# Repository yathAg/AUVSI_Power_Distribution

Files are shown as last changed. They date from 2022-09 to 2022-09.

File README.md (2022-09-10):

# AUVSI_Power_Distribution

This project includes the PCBS designed for the Seraphim , the Hex-rotor by PROJECT MANAS that participated in AUVSI SUAS 2022

The unavailibility of cheap and reliable power distribution systems called for designing a fully custom solution that powers the following :-
- Six T-Motor P60 170 Kv motors
- PixHawk Cube Orange
- RFD900X Telemetry Radio
- UGV Winch mechanism

The onboard electronic components are powered by
- Two 6S 32000 mAh LiPO Batteries for the Motors
- One 3S 4200 mAh LiPO Battery for control electronics

**The project includes three pcbs:**

## Power distribution pcb

A simple distributor pcb which can have upto 12 motors:
2 Oz thickness for more current
Exposed copper for heat sink
Voltage sense capability using the voltage from balance connector
Mosfets to shut down current flow when required

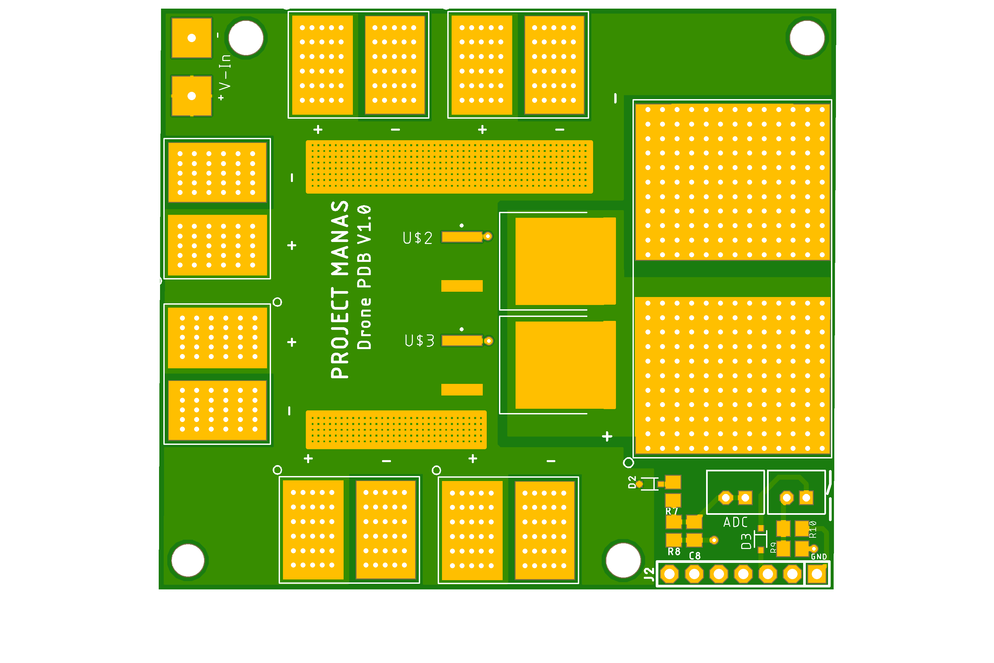
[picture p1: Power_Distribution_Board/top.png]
Power Distribution Board


## Current sensing pcb  
This pcb is based on the allegro asc772 current sensor
The 400 amp variant was avoided due to unavailability
The 200 amp variant was chosen
2 boards will be used in order to measure separate packs in parallel
Output is a analog value of 5v
The board can also measure voltage levels

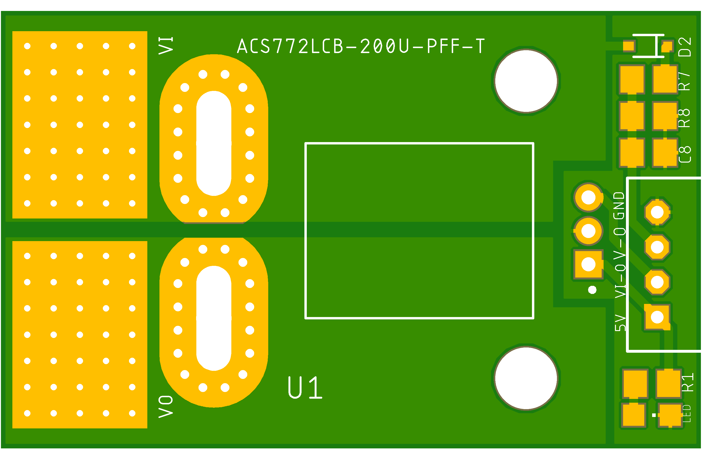
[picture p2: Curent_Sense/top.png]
Curent Sense PCB


## Power HUB

This pcb incorporates the buck and boost modules
1x5v buck ( df13)
2x 5v buck ( ph)
1x 7.4v buck
Current sense mixer

The lmr33640 ic was chosen due to wide input range and 4 amp current output
All bucks were separated
Low space design
Can mix to current sensor values using opamp circuit
Reverse polarity protection

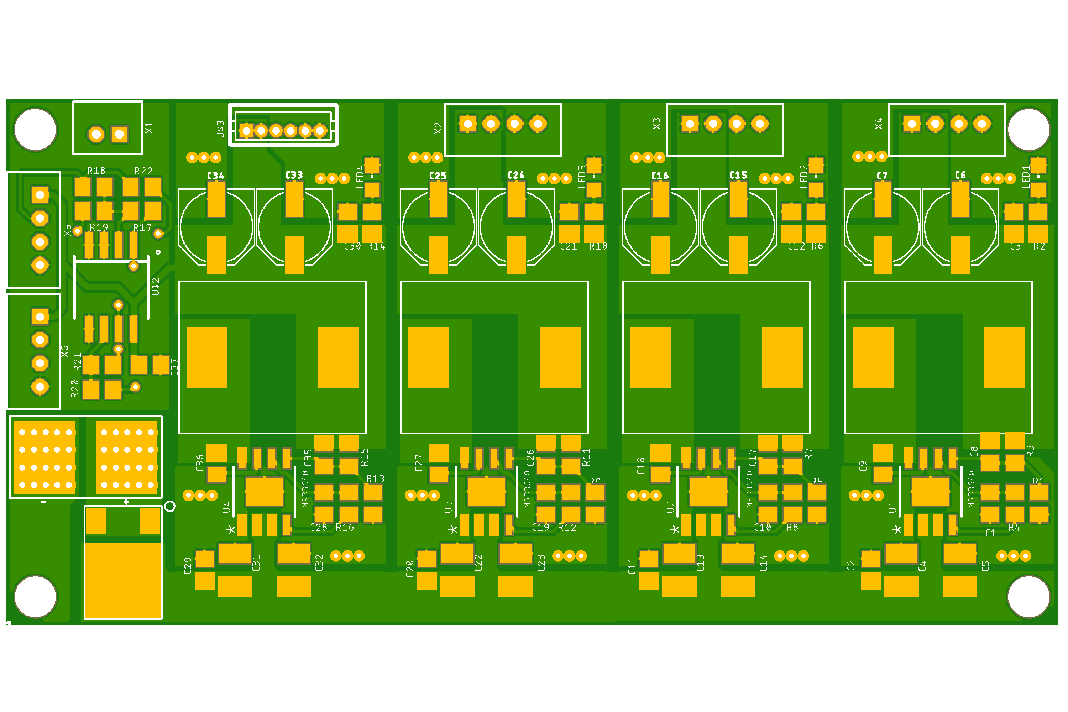
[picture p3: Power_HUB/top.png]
Power HUB


## Pcb design learnings from the project
- No thermals in high current pads
- Avoid choke points ( traces that make current flow path longer)
- Switching loops of power converters have to be as small as possible
- output trace thickness
- Placement of decoupling caps
- Using keepots to avoid traces being to close
- Appropriate pad sizes with vias for current conduction

All schematics , pcb images, and gerber files have been added
The gerbers were formatted for panelization

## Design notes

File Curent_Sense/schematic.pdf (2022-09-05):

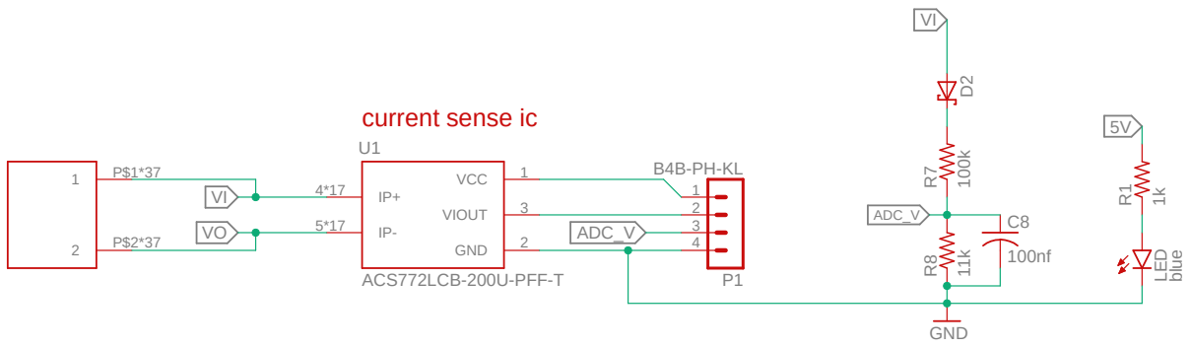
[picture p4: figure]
ACS772LCB-200U-PFF-T; GND; 1k blue; VCC; VIOUT; LED; ADC_V; current sense ic

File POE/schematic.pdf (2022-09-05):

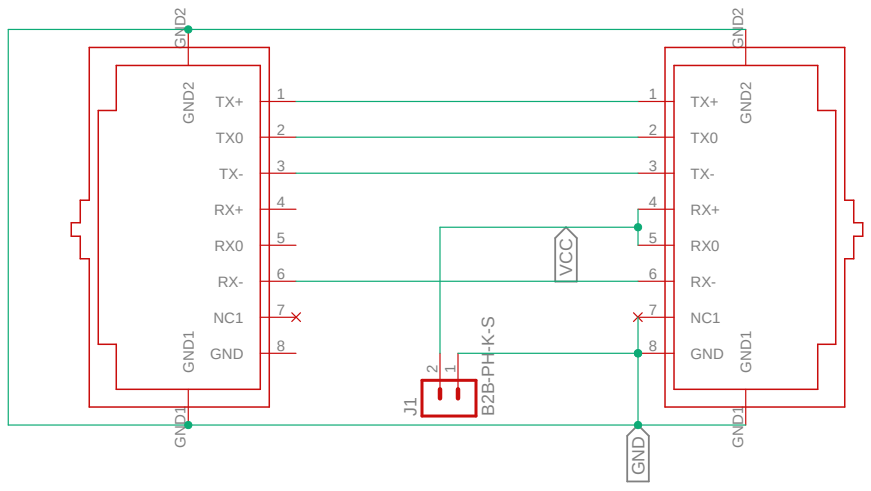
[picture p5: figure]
GND; 8 GND² GND² GND¹ GND¹; GND² GND² GND¹ GND¹ ²¹ J1; GND VCC

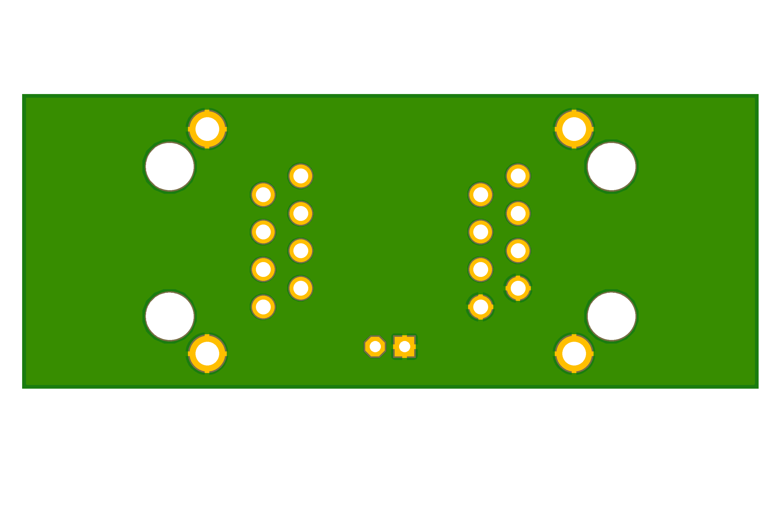
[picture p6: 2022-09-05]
POE/bottom.png

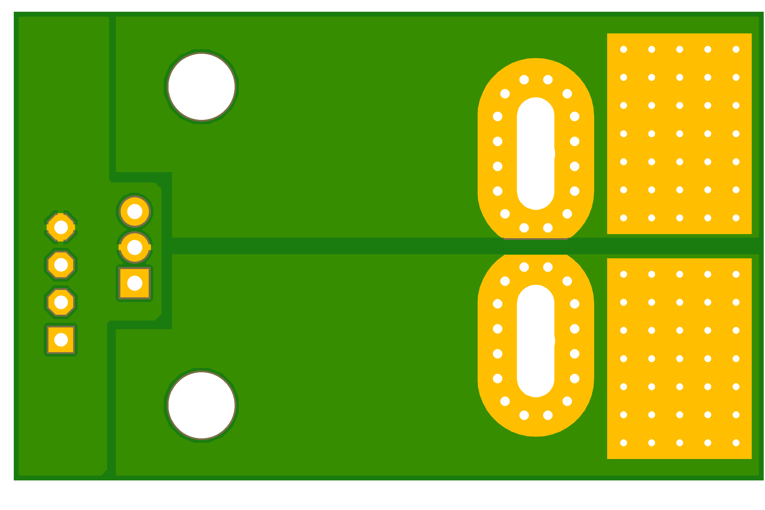
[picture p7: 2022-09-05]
Curent_Sense/bottom.png

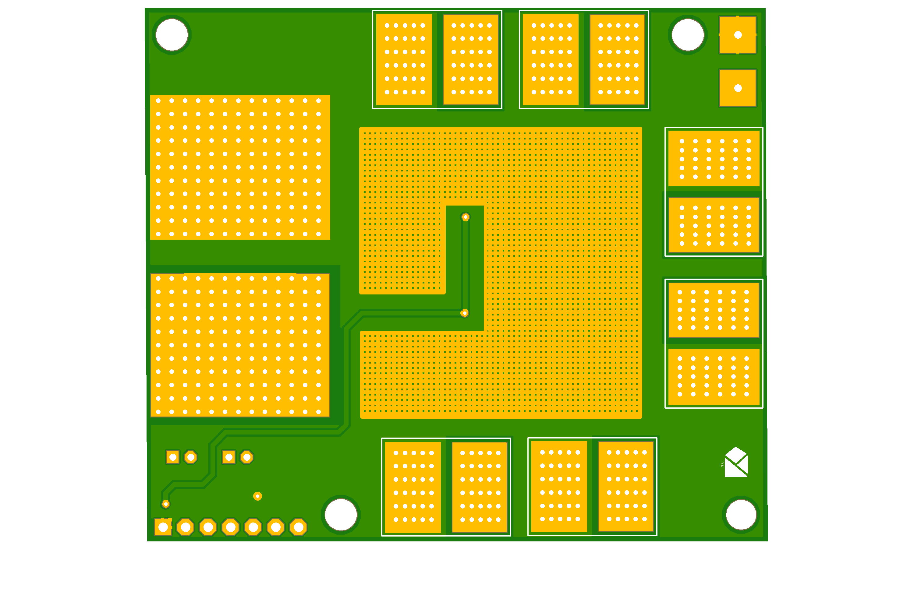
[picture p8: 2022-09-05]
Power_Distribution_Board/bottom.png

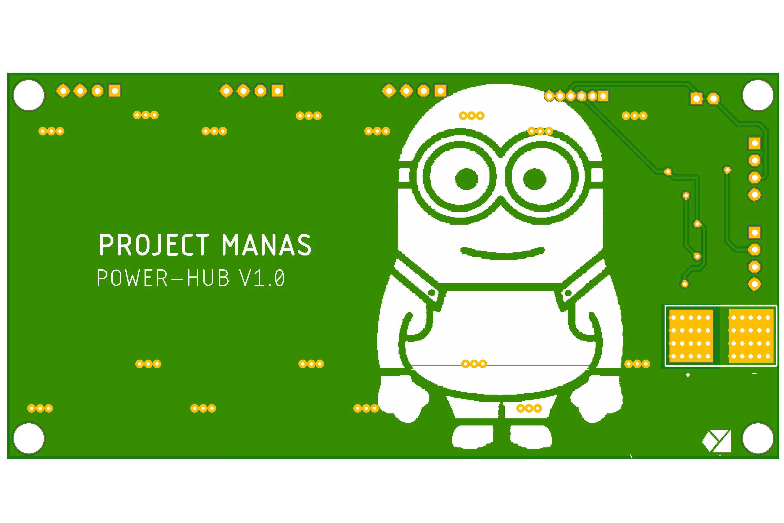
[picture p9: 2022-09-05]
Power_HUB/bottom.png

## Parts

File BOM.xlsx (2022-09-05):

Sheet: pdb
Qty | Value | Device | Package | Parts | Description
1 | 100k | R-US_R0805 | R0805 | R7 | RESISTOR, American symbol
1 | 100nf | C-USC0805 | C0805 | C8 | CAPACITOR, American symbol
1 | 11k | R-US_R0805 | R0805 | R8 | RESISTOR, American symbol
2 | 1PS76SB70,115 | 1PS76SB70,115 | SOD323(F) | D2, D3 | General-purpose Schottky diode General-purpose Schottky diodes in small Surface-Mounted Device (SMD) plastic
2 | 1k | R-US_R0805 | R0805 | R9, R10 | RESISTOR, American symbol
1 | B2B-PH-K-S | B2B-PH-K-S | B2B-PH-K-S | P2 | JST PH series header 2.00mm pitch disconnectable crimp style connectors, vertical (side entry type), 2 pins
1 | B2B-PH-KL | B2B-PH-KL | B2B-PH-K-S | P3 | JST PH series header 2.00mm pitch disconnectable crimp style connectors, vertical (side entry type), 2 pins
1 | F-1X07-SIP-100-40 | F-1X07-SIP-100-40 | SIP-100-07-40 | J2 | FEMALE HEADER
2 | IRFS7730 | IRFS7730 | TO254P1524X457-3N | U$2, U$3

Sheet: current sense
Qty | Value | Device | Package | Parts | Description
1 | 100k | R-US_R0805 | R0805 | R7 | RESISTOR, American symbol
1 | 100nf | C-USC0805 | C0805 | C8 | CAPACITOR, American symbol
1 | 11k | R-US_R0805 | R0805 | R8 | RESISTOR, American symbol
1 | 1PS76SB70,115 | 1PS76SB70,115 | SOD323(F) | D2 | General-purpose Schottky diode General-purpose Schottky diodes in small Surface-Mounted Device (SMD) plastic
1 | 1k | R-US_R0805 | R0805 | R1 | RESISTOR, American symbol
1 | ACS772LCB-200U-PFF-T | ACS772LCB-100U-PFF-T | XDCR_ACS772LCB-100U-PFF-T | U1 | Current Sensor 100A 1 Channel Hall Effect Unidirectional 5-CB Formed Leads, PFF Check prices
1 | B4B-PH-KL | B4B-PH-KL | B4B-PH-K-S | P1 | JST PH series header 2.00mm pitch disconnectable crimp style connectors, vertical (side entry type), 4 pins
1 | blue | LEDCHIPLED_0805 | CHIPLED_0805 | LED | LED

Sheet: poe
Qty | Value | Device | Package | Parts | Description
1 | B2B-PH-K-S | B2B-PH-K-S | B2B-PH-K-S | J1 | JST PH series header 2.00mm pitch disconnectable crimp style connectors, vertical (side entry type), 2 pins
2 | RJ45-TRAFO | RJ45-TRAFO | RJ45-TRAFO | U$1, U$2 | RJ45 socket with integrated magnetics

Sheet: powerhub
Qty | Value | Device | Package | Parts | Description
8 | 100k | R-US_R0805 | R0805 | R3, R4, R7, R8, R11, R12, R15, R16 | RESISTOR, American symbol
9 | 100nf | C-EUC0805 | C0805 | C3, C9, C12, C18, C21, C27, C30, C36, C37 | CAPACITOR, European symbol
8 | 100uF | 100UF-POLAR-25V-20%(ELEC) | PANASONIC_D | C6, C7, C15, C16, C24, C25, C33, C34 | 100µF polarized capacitors
8 | 10uf | C-EUC1210 | C1210 | C4, C5, C13, C14, C22, C23, C31, C32 | CAPACITOR, European symbol
1 | 10uh | INDUCTORINDUCTOR-1265 | INDUCTOR-1265 | I1 | 1260 wurth elektronics
4 | 11k | R-US_R0805 | R0805 | R17, R18, R19, R20 | RESISTOR, American symbol
1 | 15.6k | R-US_R0805 | R0805 | R1 | RESISTOR, American symbol
4 | 1k | R-US_R0805 | R0805 | R2, R6, R10, R14 | RESISTOR, American symbol
4 | 1uf | C-EUC0805 | C0805 | C1, C10, C19, C28 | CAPACITOR, European symbol
4 | 220nf | C-EUC0805 | C0805 | C2, C11, C20, C29 | CAPACITOR, European symbol
1 | 22k | R-US_R0805 | R0805 | R21 | RESISTOR, American symbol
4 | 22pf | C-EUC0805 | C0805 | C8, C17, C26, C35 | CAPACITOR, European symbol
3 | 24.9k | R-US_R0805 | R0805 | R5, R9, R13 | RESISTOR, American symbol
3 | 6.8uh | INDUCTORINDUCTOR-1265 | INDUCTOR-1265 | I2, I3, I4 | 1260 wurth elektronics
1 | B2B-PH-KL | B2B-PH-KL | B2B-PH-K-S | X1 | JST PH series header 2.00mm pitch disconnectable crimp style connectors, vertical (side entry type), 2 pins
5 | B4B-PH-KL | B4B-PH-KL | B4B-PH-K-S | X2, X3, X4, X5, X6 | JST PH series header 2.00mm pitch disconnectable crimp style connectors, vertical (side entry type), 4 pins
1 | LM358 | LM358 | SOP-08 | U$2
4 | LMR33640 | LMR33640 | SO-POWERPAD8_DDA_TEX-M | U1, U2, U3, U4
1 | V40PW22C-M3/I | DIODE-TO252 | TO-252AE | U$1
4 | blue | LEDCHIPLED_0805 | CHIPLED_0805 | LED1, LED2, LED3, LED4 | LED

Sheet: total
Qty for 1 set | Value | Device | Package | Description
10 | 100k | R-US_R0805 | R0805 | RESISTOR, American symbol
11 | 100nf | C-EUC0805 | C0805 | CAPACITOR, European symbol
8 | 100uF | 100UF-POLAR-25V-20%(ELEC) | PANASONIC_D | 100µF polarized capacitors
8 | 10uf | C-EUC1210 | C1210 | CAPACITOR, European symbol
1 | 10uh | INDUCTORINDUCTOR-1265 | INDUCTOR-1265 | 1260 wurth elektronics ( or any similar)
6 | 11k | R-US_R0805 | R0805 | RESISTOR, American symbol
1 | 15.6k | R-US_R0805 | R0805 | RESISTOR, American symbol
7 | 1k | R-US_R0805 | R0805 | RESISTOR, American symbol
4 | 1uf | C-EUC0805 | C0805 | CAPACITOR, European symbol
4 | 220nf | C-EUC0805 | C0805 | CAPACITOR, European symbol
1 | 22k | R-US_R0805 | R0805 | RESISTOR, American symbol
4 | 22pf | C-EUC0805 | C0805 | CAPACITOR, European symbol
3 | 24.9k | R-US_R0805 | R0805 | RESISTOR, American symbol
3 | 6.8uh | INDUCTORINDUCTOR-1265 | INDUCTOR-1265 | 1260 wurth elektronics ( or any similar)
1 | ACS772LCB-200U-PFF-T | ACS772LCB-100U-PFF-T | XDCR_ACS772LCB-100U-PFF-T | Current Sensor 200A 1 Channel Hall Effect Unidirectional 5-CB Formed Leads, PFF ( or any acs current sense 200 amp 712,758
4 | B2B-PH-KL | B2B-PH-KL | B2B-PH-K-S | JST PH series header 2.00mm pitch disconnectable crimp style connectors, vertical , 2 pins
6 | B4B-PH-KL | B4B-PH-KL | B4B-PH-K-S | JST PH series header 2.00mm pitch disconnectable crimp style connectors, vertical (side entry type), 4 pins ( or any similar 2mm pitch connector)
5 | blue | LEDCHIPLED_0805 | CHIPLED_0805 | LED
1 | df13
2 | IRFS7730 | IRFS7730 | TO254P1524X457-3N
1 | LM358 | LM358 | SOP-08
4 | LMR33640 | LMR33640 | SO-POWERPAD8_DDA_TEX-M
2 | RJ45-TRAFO | RJ45-TRAFO | RJ45-TRAFO | RJ45 socket with integrated magnetics
3 | schottkey diode | 1PS76SB70,115 | sod123 | General-purpose Schottky diode General-purpose Schottky diodes in small Surface-Mounted Device (SMD) plastic ( or any similar)
1 | V40PW22C-M3/I | DIODE-TO252 | TO-252AE

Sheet: ic
Value | Device | Package | qty | price
LMR33640 | LMR33640 | SO-POWERPAD8_DDA_TEX-M
IRFS7730 | IRFS7730 | TO254P1524X457-3N | 4
ACS772LCB-200U-PFF-T | ACS772LCB-200U-PFF-T | XDCR_ACS772LCB-200U-PFF-T | 2
V40PW22C-M3/I | DIODE-TO252 | TO-252AE | 4
LM358 | LM358 | SOP-08 | 1

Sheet: connectors
Connector | Quantity
Df13 | 5
XT60-Male
XT60-Female
Rj45 Male
Rj45 Female
Xt150
2pin ph
Wire to board | 15
Connector housing | 15
4pin ph
Wire to board | 20
Connector housing | 50
Crimp contacts | 100

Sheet: final smd
part | package | desc | qty | cost | total
22k | R-US_R0805 | R0805 | 100 | 0.2 | 20
100k | R-US_R0805 | R0805 | 100 | 0.2 | 20
1uf | C-EUC0805 | C0805 | 100 | 1 | 100
220nf | C-EUC0805 | C0805 | 100 | 1 | 100
22pf | C-EUC0805 | C0805 | 100 | 1 | 100
24.9k | R-US_R0805 | R0805 | 100 | 1 | 100
15.6k | R-US_R0805 | R0805 | 100 | 1 | 100
100nf | C-EUC0805 | C0805 | 100 | 1 | 100
1k | R-US_R0805 | R0805 | 100 | 1 | 100
11k | R-US_R0805 | R0805 | 100 | 1 | 100
blue | LEDCHIPLED_0805 | CHIPLED_0805 | 100 | 1 | 100
100uF | 100UF-POLAR-25V-20%(ELEC) | PANASONIC_D | 50 | 3.5 | 175
10uf | C-EUC1210 | C1210 | 50 | 4 | 200
6.8uh | INDUCTORINDUCTOR-1265 | 5a | 10 | 35 | 350
10uh | INDUCTORINDUCTOR-1265 | 5a | 5 | 35 | 175
schottkey diode |  | sod123 | 50 | 3 | 150
 |  |  |  | total | 1990

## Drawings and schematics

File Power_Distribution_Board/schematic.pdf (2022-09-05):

## motor pads

A

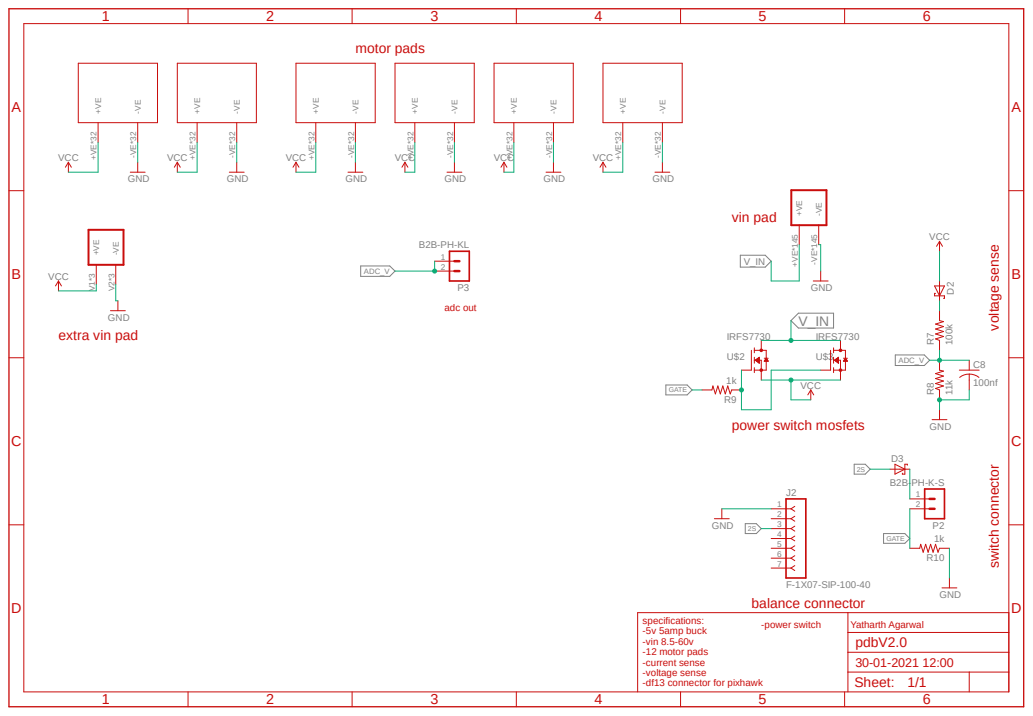
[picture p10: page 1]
VCC; GND; IRFS7730; F-1X07-SIP-100-40; ADC_V; GATE; GATE specifications:; Yatharth Agarwal; vin pad; balance connector; voltage sense; power switch mosfets; switch connector; -power switch; adc out; Sheet:; pdbV2.0

extra vin pad

-5v 5amp buck
-vin 8.5-60v
-12 motor pads
-current sense
-voltage sense
-df13 connector for pixhawk

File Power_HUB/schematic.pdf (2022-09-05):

VIN 2 | EN 3 | PG 4 | VCC 6 | PGND

A

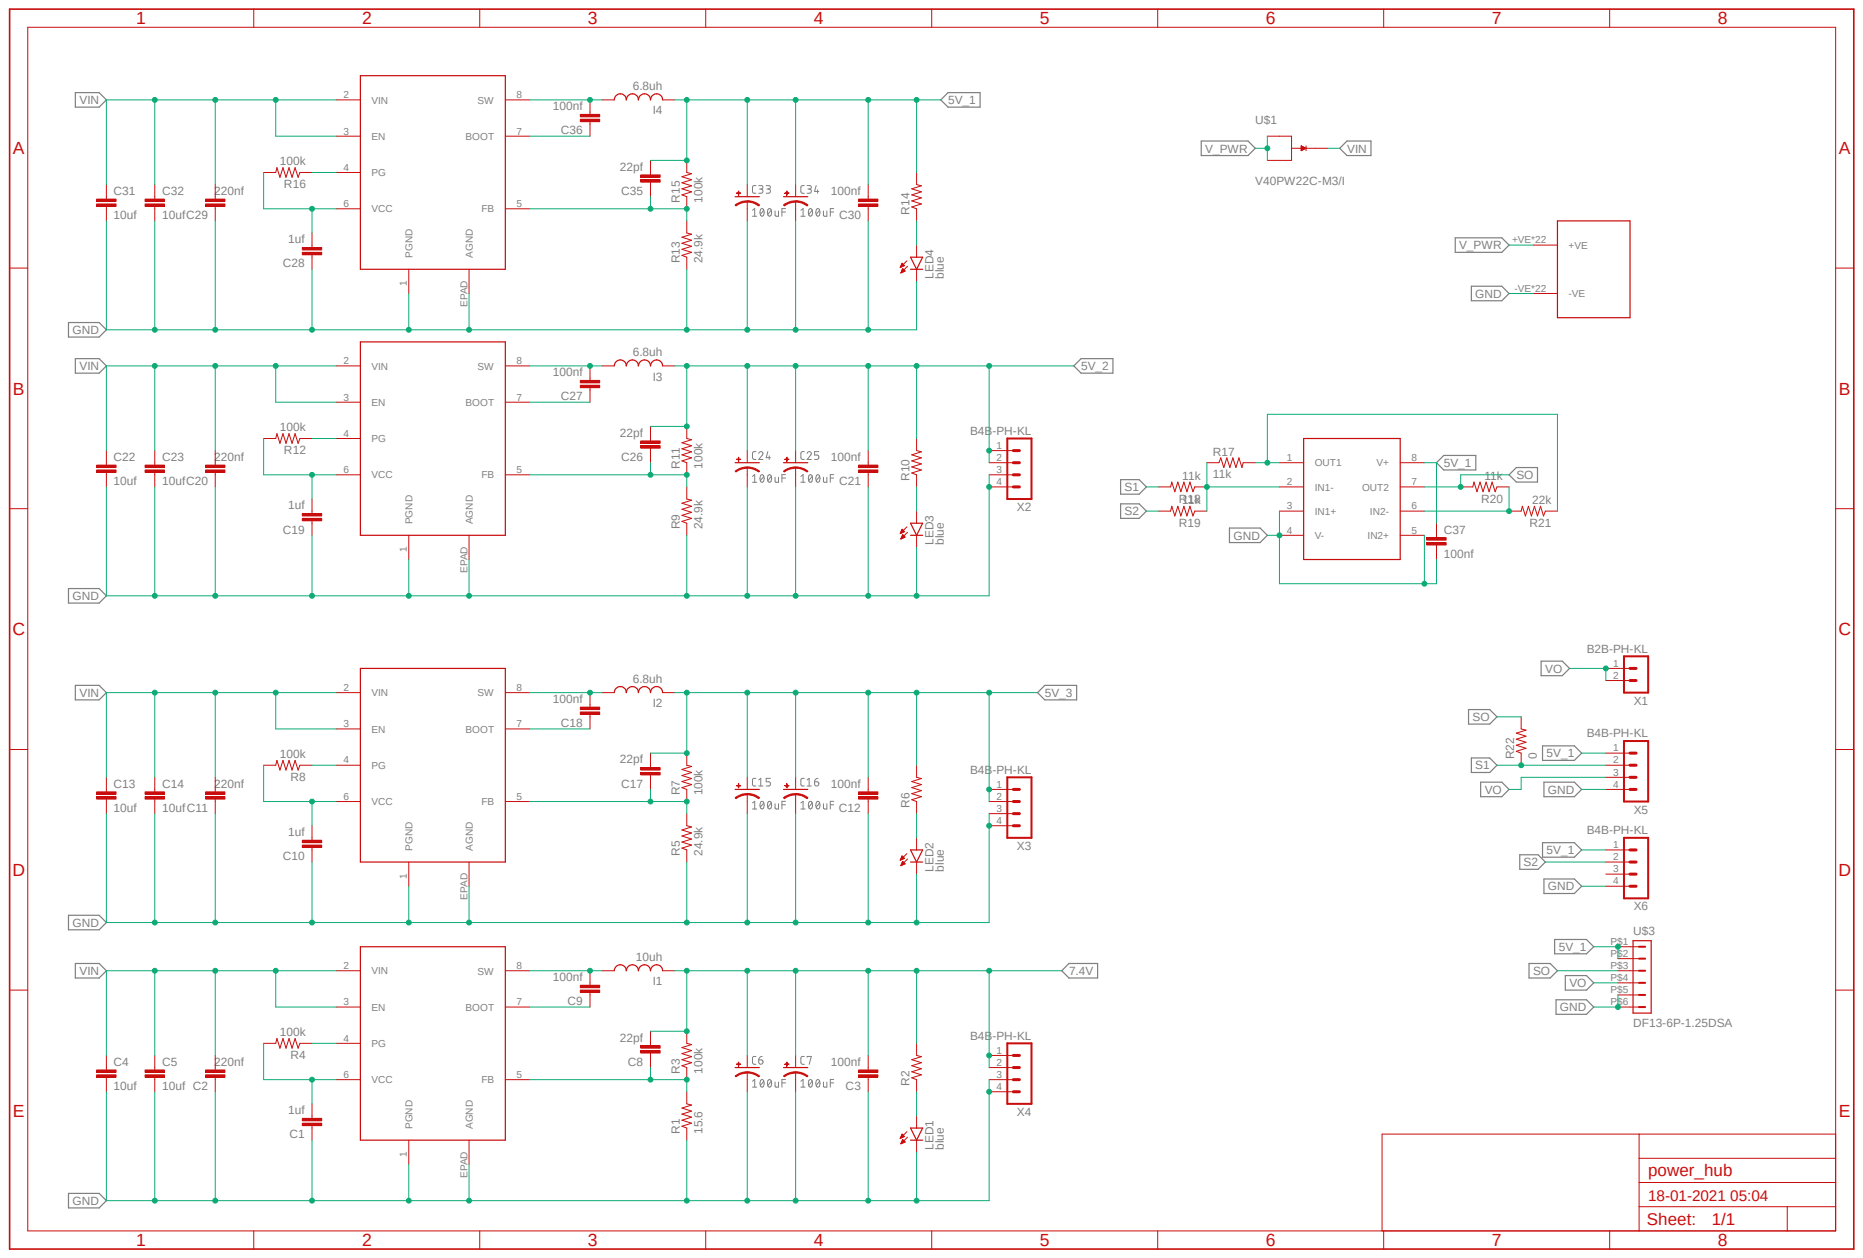
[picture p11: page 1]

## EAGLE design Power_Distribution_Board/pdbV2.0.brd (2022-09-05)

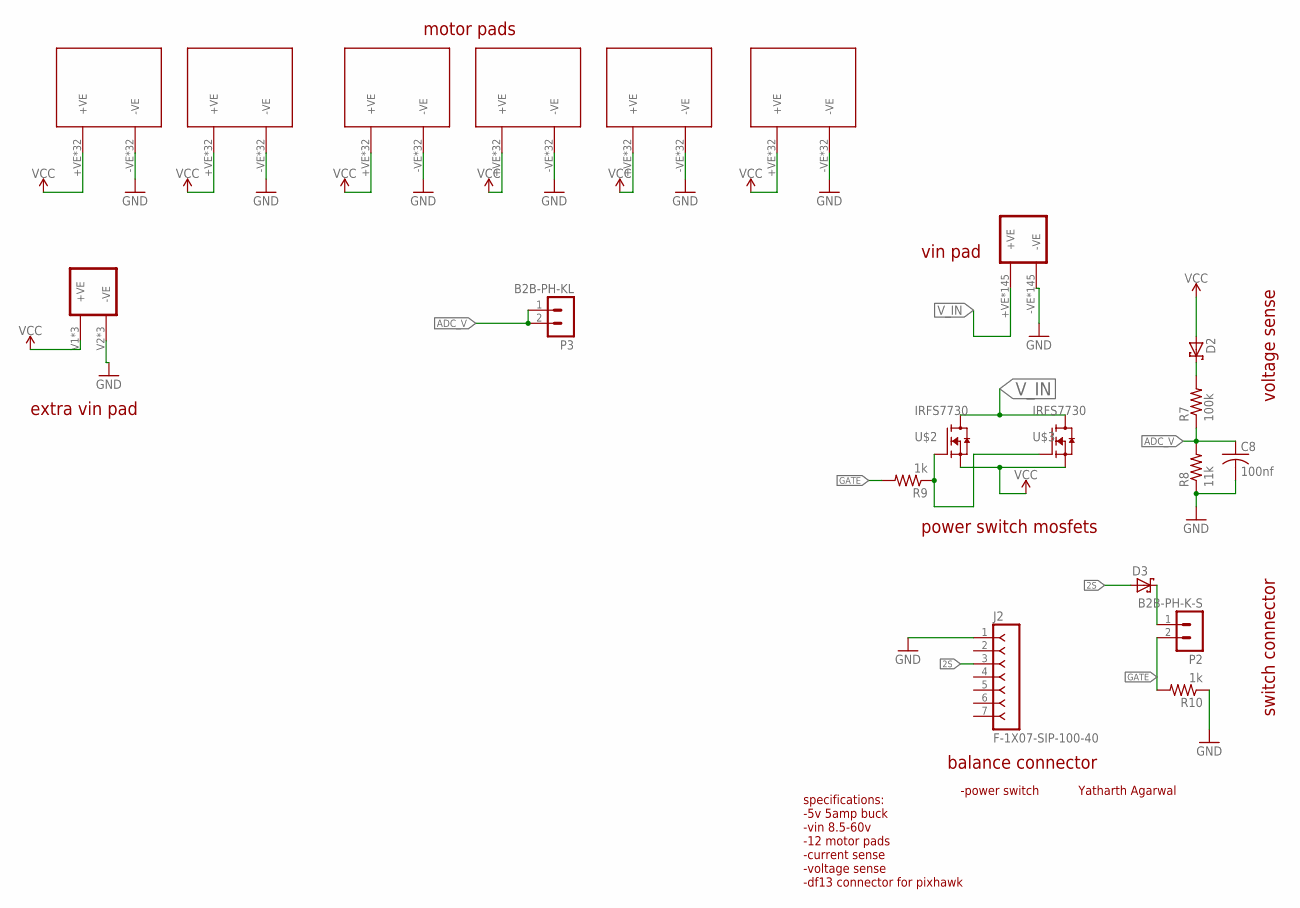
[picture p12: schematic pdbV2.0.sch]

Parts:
C8: 100nf; C0805
D2, D3: 1PS76SB70,115; SOD323(F)
J2: F-1X07-SIP-100-40; SIP-100-07-40
P2: B2B-PH-K-S
P3: B2B-PH-KL; B2B-PH-K-S
R7: 100k; R0805
R8: 11k; R0805
R9, R10: 1k; R0805
T1: BATTERY_PAD
T2, T3, T4, T5, T6, T7: MOTOR_PAD
U$1: CONPAD
U$2, U$3: IRFS7730; TO254P1524X457-3N

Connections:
2S: D3.2 (A), J2.3
ADC_V: C8.1, P3.1, P3.2, R7.1, R8.2
GATE: P2.2, R9.2, R10.2
GND: C8.2, J2.1, R8.1, R10.1, T1.-VE, T1.-VE_1 (-VE), T1.V109 (-VE), T1.V110 (-VE), T1.V111 (-VE), T1.V112 (-VE), T1.V113 (-VE), T1.V114 (-VE), T1.V115 (-VE), T1.V116 (-VE), T1.V117 (-VE), T1.V118 (-VE), T1.V119 (-VE), T1.V121 (-VE), T1.V122 (-VE), T1.V123 (-VE), T1.V124 (-VE), T1.V125 (-VE), T1.V126 (-VE), T1.V127 (-VE), T1.V128 (-VE), T1.V129 (-VE), T1.V130 (-VE), T1.V131 (-VE), T1.V133 (-VE), T1.V134 (-VE), T1.V135 (-VE), T1.V136 (-VE), T1.V137 (-VE), T1.V138 (-VE), T1.V139 (-VE), T1.V140 (-VE), T1.V141 (-VE), T1.V142 (-VE), T1.V143 (-VE), T1.V145 (-VE), T1.V146 (-VE), T1.V147 (-VE), T1.V148 (-VE), T1.V149 (-VE), T1.V150 (-VE), T1.V151 (-VE), T1.V152 (-VE), T1.V153 (-VE), T1.V154 (-VE), T1.V155 (-VE), T1.V157 (-VE), T1.V158 (-VE), T1.V159 (-VE), T1.V160 (-VE), T1.V161 (-VE), T1.V162 (-VE), T1.V163 (-VE), T1.V164 (-VE), T1.V165 (-VE), T1.V166 (-VE), T1.V167 (-VE), T1.V169 (-VE), T1.V170 (-VE), T1.V171 (-VE), T1.V172 (-VE), T1.V173 (-VE), T1.V174 (-VE), T1.V175 (-VE), T1.V176 (-VE), T1.V177 (-VE), T1.V178 (-VE), T1.V179 (-VE), T1.V181 (-VE), T1.V182 (-VE), T1.V183 (-VE), T1.V184 (-VE), T1.V185 (-VE), T1.V186 (-VE), T1.V187 (-VE), T1.V188 (-VE), T1.V189 (-VE), T1.V190 (-VE), T1.V191 (-VE), T1.V193 (-VE), T1.V194 (-VE), T1.V195 (-VE), T1.V196 (-VE), T1.V197 (-VE), T1.V198 (-VE), T1.V199 (-VE), T1.V200 (-VE), T1.V201 (-VE), T1.V202 (-VE), T1.V203 (-VE), T1.V232 (-VE), T1.V233 (-VE), T1.V234 (-VE), T1.V235 (-VE), T1.V236 (-VE), T1.V237 (-VE), T1.V238 (-VE), T1.V239 (-VE), T1.V240 (-VE), T1.V241 (-VE), T1.V242 (-VE), T1.V243 (-VE), T1.V244 (-VE), T1.V245 (-VE), T1.V246 (-VE), T1.V247 (-VE), T1.V248 (-VE), T1.V249 (-VE), T1.V250 (-VE), T1.V251 (-VE), T1.V252 (-VE), T1.V253 (-VE), T1.V254 (-VE), T1.V255 (-VE), T1.V256 (-VE), T1.V257 (-VE), T1.V258 (-VE), T1.V259 (-VE), T1.V260 (-VE), T1.V261 (-VE), T1.V262 (-VE), T1.V263 (-VE), T1.V264 (-VE), T1.V265 (-VE), T1.V266 (-VE), T1.V267 (-VE), T1.V268 (-VE), T1.V269 (-VE), T1.V270 (-VE), T1.V271 (-VE), T1.V272 (-VE), T1.V273 (-VE), T1.V274 (-VE), T1.V275 (-VE), T1.V276 (-VE), T1.V277 (-VE), T1.V278 (-VE), T1.V279 (-VE), T1.V280 (-VE), T1.V281 (-VE), T1.V282 (-VE), T1.V283 (-VE), T1.V284 (-VE), T1.V285 (-VE), T1.V286 (-VE), T2.-VE, T2.-VE_1 (-VE), T2.V32 (-VE), T2.V33 (-VE), T2.V34 (-VE), T2.V35 (-VE), T2.V36 (-VE), T2.V37 (-VE), T2.V38 (-VE), T2.V39 (-VE), T2.V40 (-VE), T2.V41 (-VE), T2.V42 (-VE), T2.V43 (-VE), T2.V44 (-VE), T2.V45 (-VE), T2.V46 (-VE), T2.V47 (-VE), T2.V48 (-VE), T2.V49 (-VE), T2.V50 (-VE), T2.V51 (-VE), T2.V52 (-VE), T2.V53 (-VE), T2.V54 (-VE), T2.V55 (-VE), T2.V56 (-VE), T2.V57 (-VE), T2.V58 (-VE), T2.V59 (-VE), T2.V60 (-VE), T2.V61 (-VE), T3.-VE, T3.-VE_1 (-VE), T3.V32 (-VE), T3.V33 (-VE), T3.V34 (-VE), T3.V35 (-VE), T3.V36 (-VE), T3.V37 (-VE), T3.V38 (-VE), T3.V39 (-VE), T3.V40 (-VE), T3.V41 (-VE), T3.V42 (-VE), T3.V43 (-VE), T3.V44 (-VE), T3.V45 (-VE), T3.V46 (-VE), T3.V47 (-VE), T3.V48 (-VE), T3.V49 (-VE), T3.V50 (-VE), T3.V51 (-VE), T3.V52 (-VE), T3.V53 (-VE), T3.V54 (-VE), T3.V55 (-VE), T3.V56 (-VE), T3.V57 (-VE), T3.V58 (-VE), T3.V59 (-VE), T3.V60 (-VE), T3.V61 (-VE), T4.-VE, T4.-VE_1 (-VE), T4.V32 (-VE), T4.V33 (-VE), T4.V34 (-VE), T4.V35 (-VE), T4.V36 (-VE), T4.V37 (-VE), T4.V38 (-VE), T4.V39 (-VE), T4.V40 (-VE), T4.V41 (-VE), T4.V42 (-VE), T4.V43 (-VE), T4.V44 (-VE), T4.V45 (-VE), T4.V46 (-VE), T4.V47 (-VE), T4.V48 (-VE), T4.V49 (-VE), T4.V50 (-VE), T4.V51 (-VE), T4.V52 (-VE), T4.V53 (-VE), T4.V54 (-VE), T4.V55 (-VE), T4.V56 (-VE), T4.V57 (-VE), T4.V58 (-VE), T4.V59 (-VE), T4.V60 (-VE), T4.V61 (-VE), T5.-VE, T5.-VE_1 (-VE), T5.V32 (-VE), T5.V33 (-VE), T5.V34 (-VE), T5.V35 (-VE), T5.V36 (-VE), T5.V37 (-VE), T5.V38 (-VE), T5.V39 (-VE), T5.V40 (-VE), T5.V41 (-VE), T5.V42 (-VE), T5.V43 (-VE), T5.V44 (-VE), T5.V45 (-VE), T5.V46 (-VE), T5.V47 (-VE), T5.V48 (-VE), T5.V49 (-VE), T5.V50 (-VE), T5.V51 (-VE), T5.V52 (-VE), T5.V53 (-VE), T5.V54 (-VE), T5.V55 (-VE), T5.V56 (-VE), T5.V57 (-VE), T5.V58 (-VE), T5.V59 (-VE), T5.V60 (-VE), T5.V61 (-VE), T6.-VE, T6.-VE_1 (-VE), T6.V32 (-VE), T6.V33 (-VE), T6.V34 (-VE), T6.V35 (-VE), T6.V36 (-VE), T6.V37 (-VE), T6.V38 (-VE), T6.V39 (-VE), T6.V40 (-VE), T6.V41 (-VE), T6.V42 (-VE), T6.V43 (-VE), T6.V44 (-VE), T6.V45 (-VE), T6.V46 (-VE), T6.V47 (-VE), T6.V48 (-VE), T6.V49 (-VE), T6.V50 (-VE), T6.V51 (-VE), T6.V52 (-VE), T6.V53 (-VE), T6.V54 (-VE), T6.V55 (-VE), T6.V56 (-VE), T6.V57 (-VE), T6.V58 (-VE), T6.V59 (-VE), T6.V60 (-VE), T6.V61 (-VE), T7.-VE, T7.-VE_1 (-VE), T7.V32 (-VE), T7.V33 (-VE), T7.V34 (-VE), T7.V35 (-VE), T7.V36 (-VE), T7.V37 (-VE), T7.V38 (-VE), T7.V39 (-VE), T7.V40 (-VE), T7.V41 (-VE), T7.V42 (-VE), T7.V43 (-VE), T7.V44 (-VE), T7.V45 (-VE), T7.V46 (-VE), T7.V47 (-VE), T7.V48 (-VE), T7.V49 (-VE), T7.V50 (-VE), T7.V51 (-VE), T7.V52 (-VE), T7.V53 (-VE), T7.V54 (-VE), T7.V55 (-VE), T7.V56 (-VE), T7.V57 (-VE), T7.V58 (-VE), T7.V59 (-VE), T7.V60 (-VE), T7.V61 (-VE), U$1.V2 (-VE), U$1.V4 (-VE), U$1.V6 (-VE)
unnamed: D3.1 (K), P2.1
unnamed: D2.1 (K), R7.2
unnamed: R9.1, U$2.1 (G), U$3.1 (G)
VCC: D2.2 (A), T2.+VE, T2.+VE_1 (+VE), T2.V1 (+VE), T2.V3 (+VE), T2.V4 (+VE), T2.V5 (+VE), T2.V6 (+VE), T2.V7 (+VE), T2.V8 (+VE), T2.V9 (+VE), T2.V10 (+VE), T2.V11 (+VE), T2.V12 (+VE), T2.V13 (+VE), T2.V14 (+VE), T2.V15 (+VE), T2.V16 (+VE), T2.V17 (+VE), T2.V18 (+VE), T2.V19 (+VE), T2.V20 (+VE), T2.V21 (+VE), T2.V22 (+VE), T2.V23 (+VE), T2.V24 (+VE), T2.V25 (+VE), T2.V26 (+VE), T2.V27 (+VE), T2.V28 (+VE), T2.V29 (+VE), T2.V30 (+VE), T2.V31 (+VE), T3.+VE, T3.+VE_1 (+VE), T3.V1 (+VE), T3.V3 (+VE), T3.V4 (+VE), T3.V5 (+VE), T3.V6 (+VE), T3.V7 (+VE), T3.V8 (+VE), T3.V9 (+VE), T3.V10 (+VE), T3.V11 (+VE), T3.V12 (+VE), T3.V13 (+VE), T3.V14 (+VE), T3.V15 (+VE), T3.V16 (+VE), T3.V17 (+VE), T3.V18 (+VE), T3.V19 (+VE), T3.V20 (+VE), T3.V21 (+VE), T3.V22 (+VE), T3.V23 (+VE), T3.V24 (+VE), T3.V25 (+VE), T3.V26 (+VE), T3.V27 (+VE), T3.V28 (+VE), T3.V29 (+VE), T3.V30 (+VE), T3.V31 (+VE), T4.+VE, T4.+VE_1 (+VE), T4.V1 (+VE), T4.V3 (+VE), T4.V4 (+VE), T4.V5 (+VE), T4.V6 (+VE), T4.V7 (+VE), T4.V8 (+VE), T4.V9 (+VE), T4.V10 (+VE), T4.V11 (+VE), T4.V12 (+VE), T4.V13 (+VE), T4.V14 (+VE), T4.V15 (+VE), T4.V16 (+VE), T4.V17 (+VE), T4.V18 (+VE), T4.V19 (+VE), T4.V20 (+VE), T4.V21 (+VE), T4.V22 (+VE), T4.V23 (+VE), T4.V24 (+VE), T4.V25 (+VE), T4.V26 (+VE), T4.V27 (+VE), T4.V28 (+VE), T4.V29 (+VE), T4.V30 (+VE), T4.V31 (+VE), T5.+VE, T5.+VE_1 (+VE), T5.V1 (+VE), T5.V3 (+VE), T5.V4 (+VE), T5.V5 (+VE), T5.V6 (+VE), T5.V7 (+VE), T5.V8 (+VE), T5.V9 (+VE), T5.V10 (+VE), T5.V11 (+VE), T5.V12 (+VE), T5.V13 (+VE), T5.V14 (+VE), T5.V15 (+VE), T5.V16 (+VE), T5.V17 (+VE), T5.V18 (+VE), T5.V19 (+VE), T5.V20 (+VE), T5.V21 (+VE), T5.V22 (+VE), T5.V23 (+VE), T5.V24 (+VE), T5.V25 (+VE), T5.V26 (+VE), T5.V27 (+VE), T5.V28 (+VE), T5.V29 (+VE), T5.V30 (+VE), T5.V31 (+VE), T6.+VE, T6.+VE_1 (+VE), T6.V1 (+VE), T6.V3 (+VE), T6.V4 (+VE), T6.V5 (+VE), T6.V6 (+VE), T6.V7 (+VE), T6.V8 (+VE), T6.V9 (+VE), T6.V10 (+VE), T6.V11 (+VE), T6.V12 (+VE), T6.V13 (+VE), T6.V14 (+VE), T6.V15 (+VE), T6.V16 (+VE), T6.V17 (+VE), T6.V18 (+VE), T6.V19 (+VE), T6.V20 (+VE), T6.V21 (+VE), T6.V22 (+VE), T6.V23 (+VE), T6.V24 (+VE), T6.V25 (+VE), T6.V26 (+VE), T6.V27 (+VE), T6.V28 (+VE), T6.V29 (+VE), T6.V30 (+VE), T6.V31 (+VE), T7.+VE, T7.+VE_1 (+VE), T7.V1 (+VE), T7.V3 (+VE), T7.V4 (+VE), T7.V5 (+VE), T7.V6 (+VE), T7.V7 (+VE), T7.V8 (+VE), T7.V9 (+VE), T7.V10 (+VE), T7.V11 (+VE), T7.V12 (+VE), T7.V13 (+VE), T7.V14 (+VE), T7.V15 (+VE), T7.V16 (+VE), T7.V17 (+VE), T7.V18 (+VE), T7.V19 (+VE), T7.V20 (+VE), T7.V21 (+VE), T7.V22 (+VE), T7.V23 (+VE), T7.V24 (+VE), T7.V25 (+VE), T7.V26 (+VE), T7.V27 (+VE), T7.V28 (+VE), T7.V29 (+VE), T7.V30 (+VE), T7.V31 (+VE), U$1.V1 (+VE), U$1.V3 (+VE), U$1.V5 (+VE), U$2.3 (S), U$3.3 (S)
V_IN: T1.+VE, T1.+VE_1 (+VE), T1.V1 (+VE), T1.V2 (+VE), T1.V3 (+VE), T1.V4 (+VE), T1.V5 (+VE), T1.V6 (+VE), T1.V7 (+VE), T1.V8 (+VE), T1.V9 (+VE), T1.V10 (+VE), T1.V11 (+VE), T1.V12 (+VE), T1.V13 (+VE), T1.V14 (+VE), T1.V15 (+VE), T1.V16 (+VE), T1.V17 (+VE), T1.V18 (+VE), T1.V19 (+VE), T1.V20 (+VE), T1.V21 (+VE), T1.V22 (+VE), T1.V23 (+VE), T1.V24 (+VE), T1.V25 (+VE), T1.V26 (+VE), T1.V27 (+VE), T1.V28 (+VE), T1.V29 (+VE), T1.V30 (+VE), T1.V31 (+VE), T1.V32 (+VE), T1.V33 (+VE), T1.V34 (+VE), T1.V35 (+VE), T1.V36 (+VE), T1.V37 (+VE), T1.V38 (+VE), T1.V39 (+VE), T1.V40 (+VE), T1.V41 (+VE), T1.V42 (+VE), T1.V43 (+VE), T1.V44 (+VE), T1.V45 (+VE), T1.V46 (+VE), T1.V47 (+VE), T1.V48 (+VE), T1.V49 (+VE), T1.V50 (+VE), T1.V51 (+VE), T1.V52 (+VE), T1.V53 (+VE), T1.V54 (+VE), T1.V55 (+VE), T1.V56 (+VE), T1.V57 (+VE), T1.V58 (+VE), T1.V59 (+VE), T1.V60 (+VE), T1.V61 (+VE), T1.V62 (+VE), T1.V63 (+VE), T1.V64 (+VE), T1.V65 (+VE), T1.V66 (+VE), T1.V67 (+VE), T1.V68 (+VE), T1.V69 (+VE), T1.V70 (+VE), T1.V71 (+VE), T1.V72 (+VE), T1.V73 (+VE), T1.V74 (+VE), T1.V75 (+VE), T1.V76 (+VE), T1.V77 (+VE), T1.V78 (+VE), T1.V79 (+VE), T1.V80 (+VE), T1.V81 (+VE), T1.V82 (+VE), T1.V83 (+VE), T1.V84 (+VE), T1.V85 (+VE), T1.V86 (+VE), T1.V87 (+VE), T1.V88 (+VE), T1.V89 (+VE), T1.V90 (+VE), T1.V91 (+VE), T1.V92 (+VE), T1.V93 (+VE), T1.V94 (+VE), T1.V95 (+VE), T1.V96 (+VE), T1.V97 (+VE), T1.V98 (+VE), T1.V99 (+VE), T1.V100 (+VE), T1.V101 (+VE), T1.V102 (+VE), T1.V103 (+VE), T1.V104 (+VE), T1.V105 (+VE), T1.V106 (+VE), T1.V107 (+VE), T1.V108 (+VE), T1.V120 (+VE), T1.V132 (+VE), T1.V144 (+VE), T1.V156 (+VE), T1.V168 (+VE), T1.V180 (+VE), T1.V192 (+VE), T1.V204 (+VE), T1.V205 (+VE), T1.V206 (+VE), T1.V207 (+VE), T1.V208 (+VE), T1.V209 (+VE), T1.V210 (+VE), T1.V211 (+VE), T1.V212 (+VE), T1.V213 (+VE), T1.V214 (+VE), T1.V215 (+VE), T1.V216 (+VE), T1.V217 (+VE), T1.V218 (+VE), T1.V219 (+VE), T1.V220 (+VE), T1.V221 (+VE), T1.V222 (+VE), T1.V223 (+VE), T1.V224 (+VE), T1.V225 (+VE), T1.V226 (+VE), T1.V227 (+VE), T1.V228 (+VE), T1.V229 (+VE), T1.V230 (+VE), T1.V231 (+VE), U$2.2 (D), U$3.2 (D)

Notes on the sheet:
specifications: -5v 5amp buck -vin 8.5-60v -12 motor pads -current sense -voltage sense -df13 connector for pixhawk
Yatharth Agarwal
motor pads
extra vin pad
vin pad
balance connector
voltage sense
power switch mosfets
switch connector
-power switch

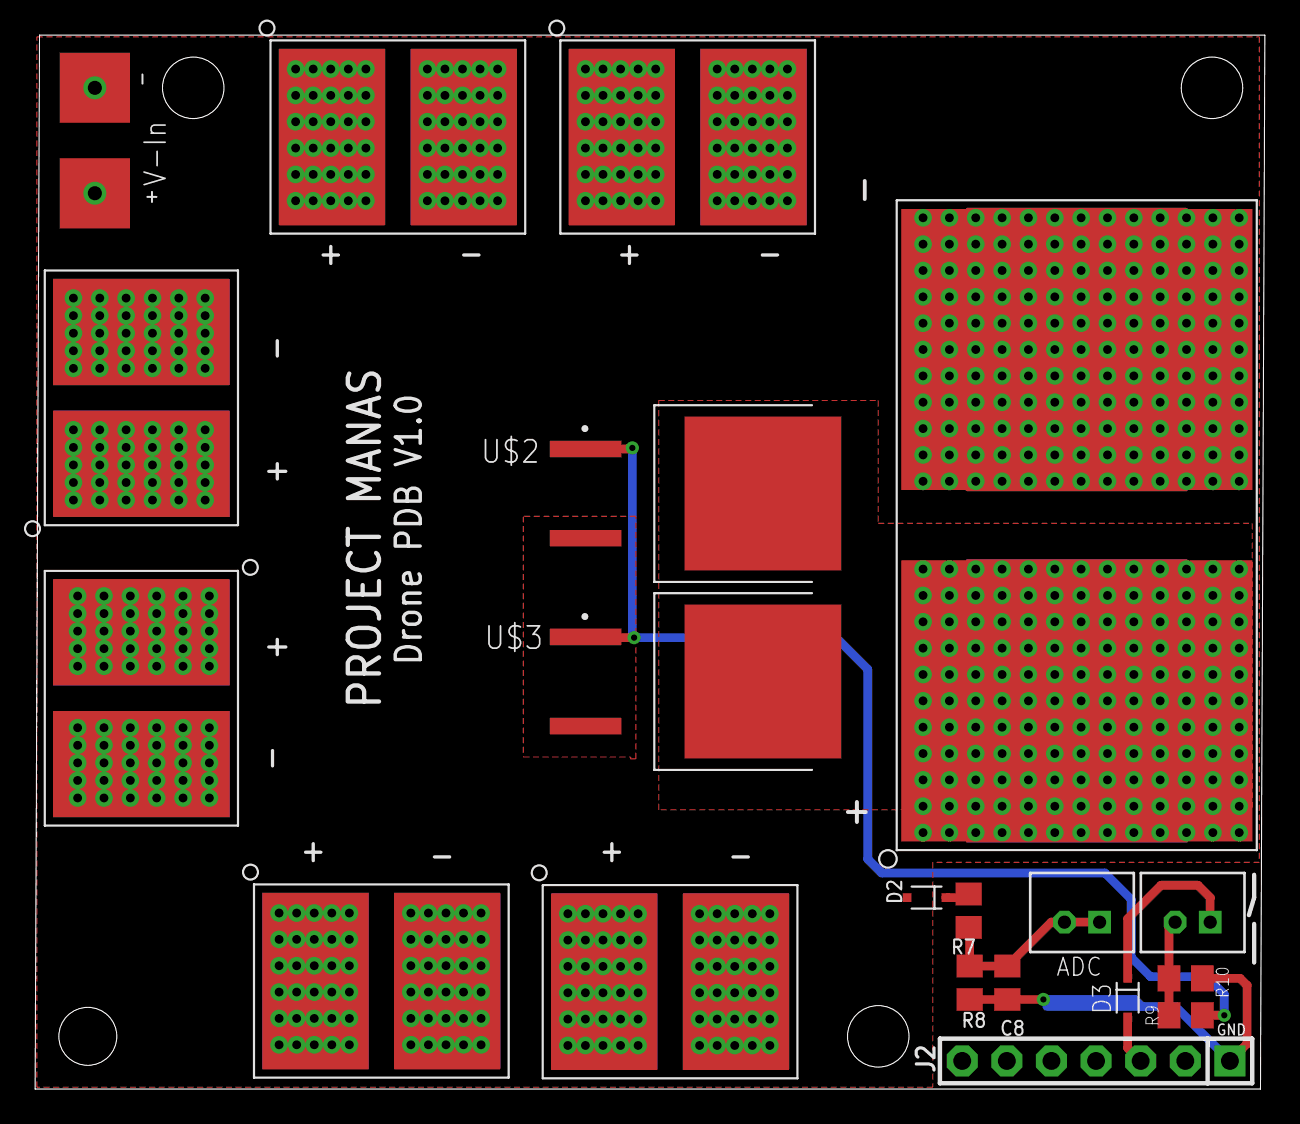
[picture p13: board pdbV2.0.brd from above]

Board: 2 copper layers, 70.0 x 60.0 mm, 20 parts (0 on the bottom side), 9 nets.

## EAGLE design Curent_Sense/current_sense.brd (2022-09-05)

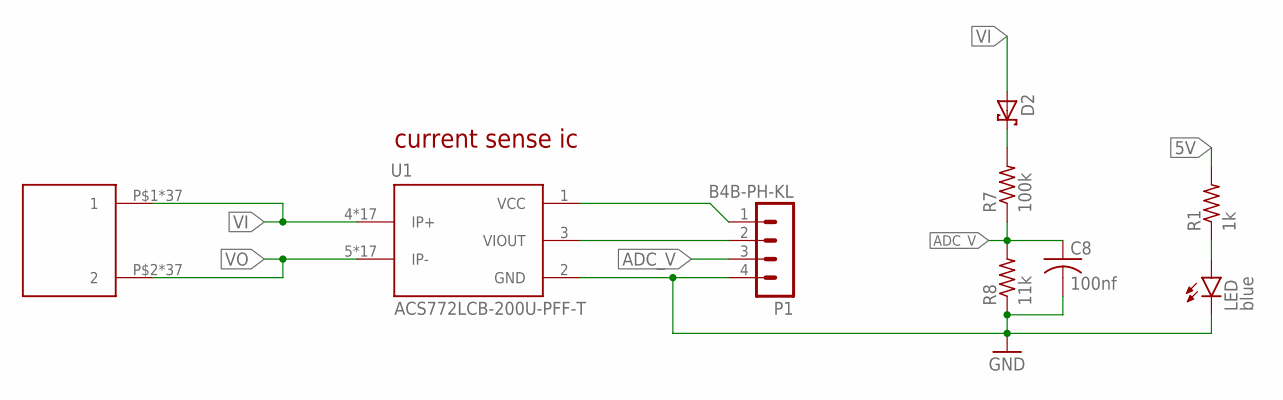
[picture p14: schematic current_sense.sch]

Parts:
C8: 100nf; C0805
D2: 1PS76SB70,115; SOD323(F)
LED: blue; CHIPLED_0805
P1: B4B-PH-KL; B4B-PH-K-S
R1: 1k; R0805
R7: 100k; R0805
R8: 11k; R0805
U1: ACS772LCB-200U-PFF-T; XDCR_ACS772LCB-100U-PFF-T
U$1: CON_PAD

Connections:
5V: P1.1, R1.2, U1.1 (VCC)
ADC_V: C8.1, P1.3, R7.1, R8.2
GND: C8.2, LED.C, P1.4, R8.1, U1.2 (GND)
unnamed: P1.2, U1.3 (VIOUT)
unnamed: LED.A, R1.1
unnamed: D2.1 (K), R7.2
VI: D2.2 (A), U1.4 (IP+), U1.4_1 (IP+), U1.4_2 (IP+), U1.4_3 (IP+), U1.4_4 (IP+), U1.4_5 (IP+), U1.4_6 (IP+), U1.4_7 (IP+), U1.4_8 (IP+), U1.4_9 (IP+), U1.4_10 (IP+), U1.4_11 (IP+), U1.4_12 (IP+), U1.4_13 (IP+), U1.4_14 (IP+), U1.4_15 (IP+), U1.4_16 (IP+), U$1.P$1 (1), U$1.P$3 (1), U$1.P$5 (1), U$1.P$6 (1), U$1.P$7 (1), U$1.P$8 (1), U$1.P$9 (1), U$1.P$10 (1), U$1.P$11 (1), U$1.P$12 (1), U$1.P$13 (1), U$1.P$14 (1), U$1.P$15 (1), U$1.P$16 (1), U$1.P$17 (1), U$1.P$18 (1), U$1.P$19 (1), U$1.P$20 (1), U$1.P$21 (1), U$1.P$22 (1), U$1.P$23 (1), U$1.P$24 (1), U$1.P$25 (1), U$1.P$26 (1), U$1.P$27 (1), U$1.P$28 (1), U$1.P$29 (1), U$1.P$30 (1), U$1.P$31 (1), U$1.P$32 (1), U$1.P$33 (1), U$1.P$34 (1), U$1.P$35 (1), U$1.P$36 (1), U$1.P$37 (1), U$1.P$38 (1), U$1.P$39 (1)
VO: U1.5 (IP-), U1.5_1 (IP-), U1.5_2 (IP-), U1.5_3 (IP-), U1.5_4 (IP-), U1.5_5 (IP-), U1.5_6 (IP-), U1.5_7 (IP-), U1.5_8 (IP-), U1.5_9 (IP-), U1.5_10 (IP-), U1.5_11 (IP-), U1.5_12 (IP-), U1.5_13 (IP-), U1.5_14 (IP-), U1.5_15 (IP-), U1.5_16 (IP-), U$1.P$2 (2), U$1.P$4 (2), U$1.P$40 (2), U$1.P$41 (2), U$1.P$42 (2), U$1.P$43 (2), U$1.P$44 (2), U$1.P$45 (2), U$1.P$46 (2), U$1.P$47 (2), U$1.P$48 (2), U$1.P$49 (2), U$1.P$50 (2), U$1.P$51 (2), U$1.P$52 (2), U$1.P$53 (2), U$1.P$54 (2), U$1.P$55 (2), U$1.P$56 (2), U$1.P$57 (2), U$1.P$58 (2), U$1.P$59 (2), U$1.P$60 (2), U$1.P$61 (2), U$1.P$62 (2), U$1.P$63 (2), U$1.P$64 (2), U$1.P$65 (2), U$1.P$66 (2), U$1.P$67 (2), U$1.P$68 (2), U$1.P$69 (2), U$1.P$70 (2), U$1.P$71 (2), U$1.P$72 (2), U$1.P$73 (2), U$1.P$74 (2)

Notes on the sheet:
current sense ic

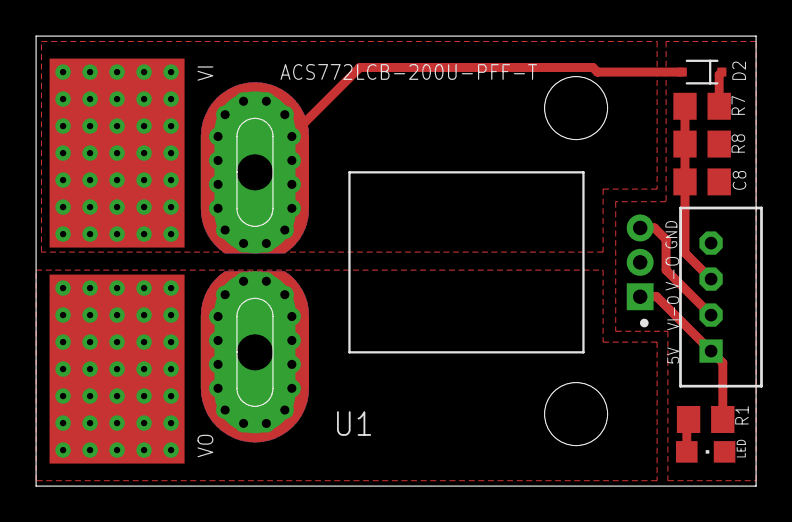
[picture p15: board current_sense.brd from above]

Board: 2 copper layers, 40.0 x 25.0 mm, 9 parts (0 on the bottom side), 8 nets.

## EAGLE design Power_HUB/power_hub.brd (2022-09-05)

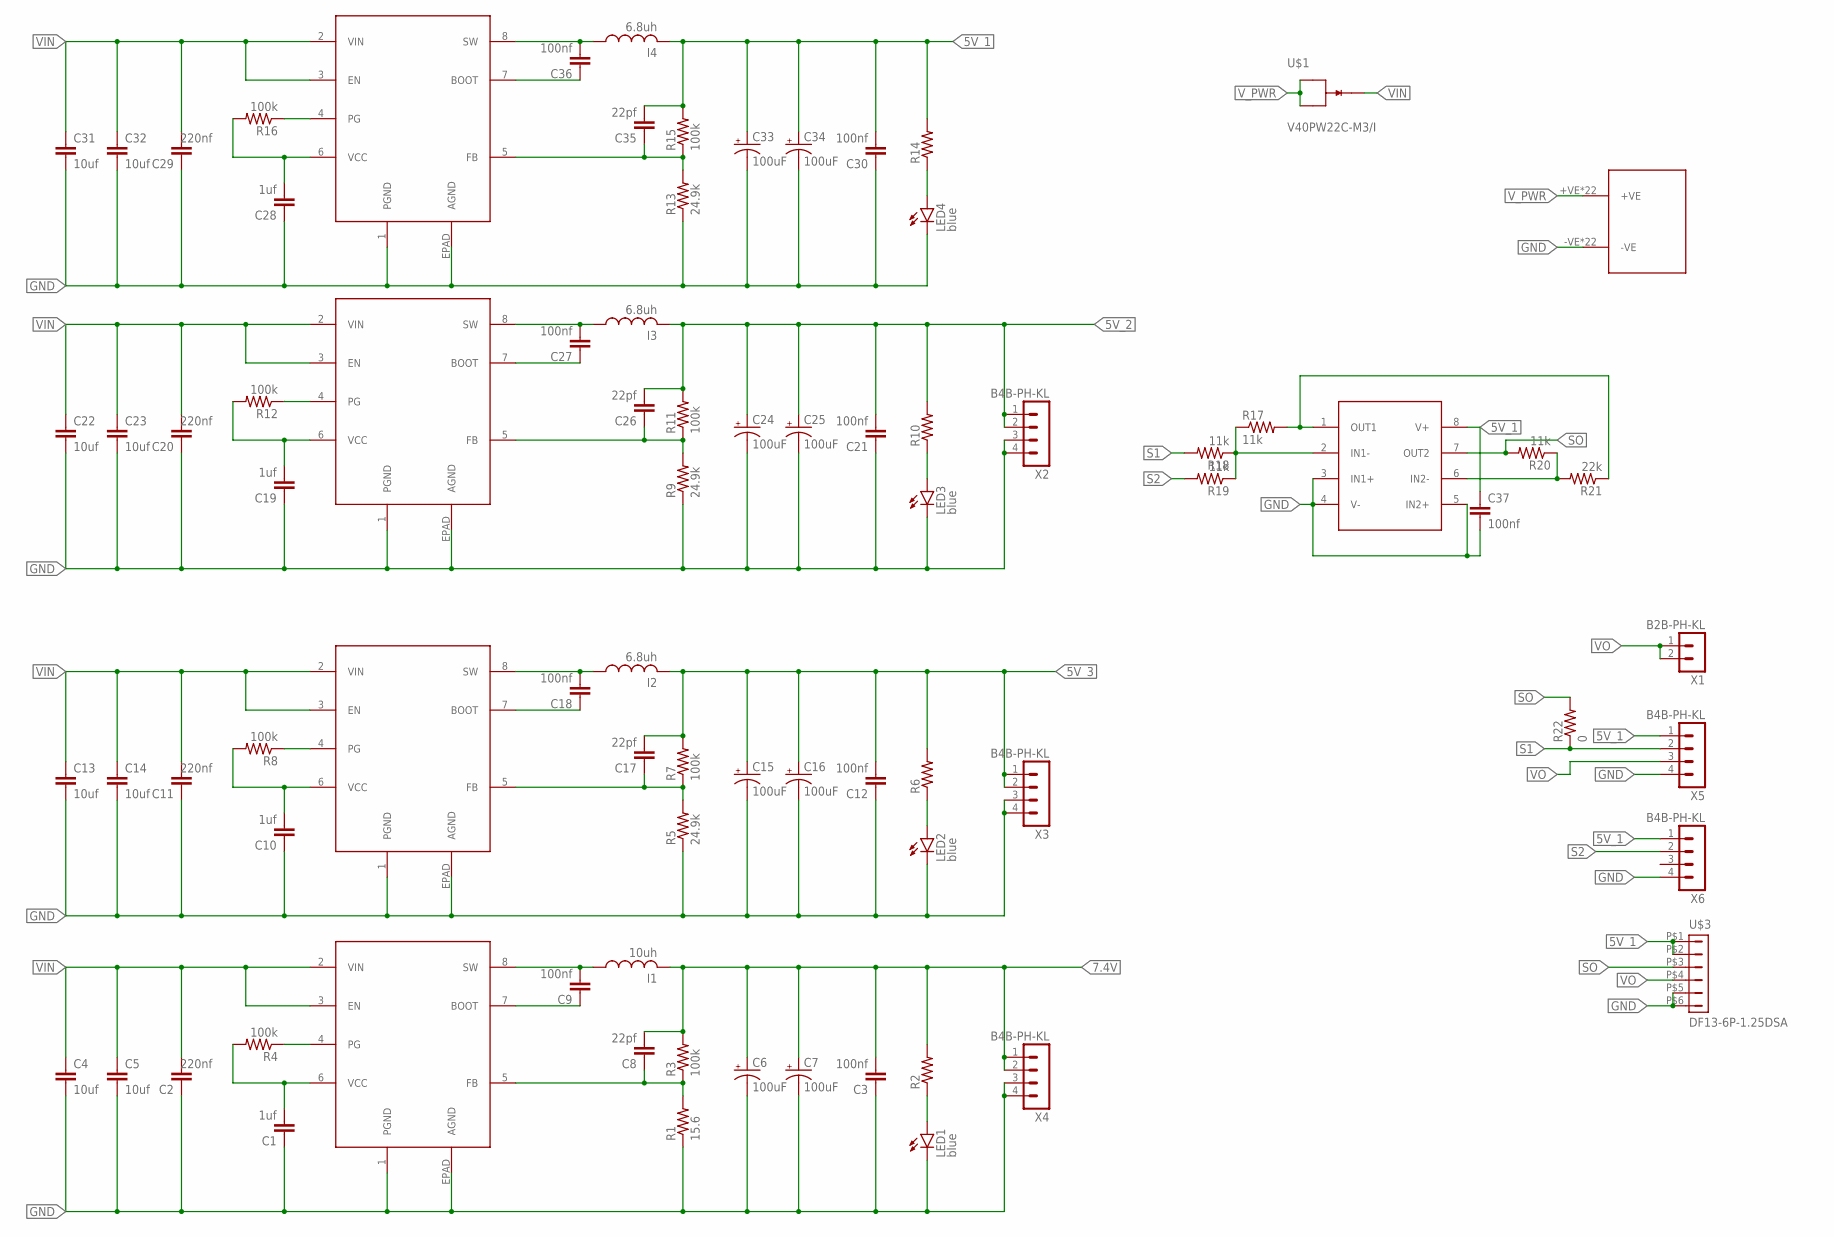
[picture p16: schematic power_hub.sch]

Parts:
C1, C10, C19, C28: 1uf; C0805
C2, C11, C20, C29: 220nf; C0805
C3, C9, C12, C18, C21, C27, C30, C36, C37: 100nf; C0805
C4, C5, C13, C14, C22, C23, C31, C32: 10uf; C1210
C6, C7, C15, C16, C24, C25, C33, C34: 100uF; PANASONIC_D
C8, C17, C26, C35: 22pf; C0805
I1: 10uh; INDUCTOR-1265
I2, I3, I4: 6.8uh; INDUCTOR-1265
LED1, LED2, LED3, LED4: blue; CHIPLED_0805
R1: 15.6; R0805
R2, R6, R10, R14: 1k; R0805
R3, R4, R7, R8, R11, R12, R15, R16: 100k; R0805
R5, R9, R13: 24.9k; R0805
R17, R18, R19, R20: 11k; R0805
R21: 22k; R0805
R22: 0; R0805
U1, U2, U3, U4: LMR33640; SO-POWERPAD8_DDA_TEX-M
U$1: V40PW22C-M3/I; TO-252AE
U$2: LM3588; SOP-08
U$3: DF13-6P-1.25DSA
U$4: CON_PAD; MOTOR_PAD
X1: B2B-PH-KL; B2B-PH-K-S
X2, X3, X4, X5, X6: B4B-PH-KL; B4B-PH-K-S

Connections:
5V_1: C30.2, C33.+, C34.+, C35.2, C37.1, I4.P$2 (2), R14.2, R15.2, U$2.8 (V+), U$3.P$1 (1), U$3.P$2 (2), X5.1, X6.1
5V_2: C21.2, C24.+, C25.+, C26.2, I3.P$2 (2), R10.2, R11.2, X2.1, X2.2
5V_3: C12.2, C15.+, C16.+, C17.2, I2.P$2 (2), R6.2, R7.2, X3.1, X3.2
7.4V: C3.2, C6.+, C7.+, C8.2, I1.P$2 (2), R2.2, R3.2, X4.1, X4.2
GND: C1.1, C2.1, C3.1, C4.2, C5.2, C6.-, C7.-, C10.1, C11.1, C12.1, C13.2, C14.2, C15.-, C16.-, C19.1, C20.1, C21.1, C22.2, C23.2, C24.-, C25.-, C28.1, C29.1, C30.1, C31.2, C32.2, C33.-, C34.-, C37.2, LED1.C, LED2.C, LED3.C, LED4.C, R1.1, R5.1, R9.1, R13.1, U1.1 (PGND), U1.EPAD (AGND), U2.1 (PGND), U2.EPAD (AGND), U3.1 (PGND), U3.EPAD (AGND), U4.1 (PGND), U4.EPAD (AGND), U$2.3 (IN1+), U$2.4 (V-), U$2.5 (IN2+), U$3.P$5 (5), U$3.P$6 (6), U$4.-VE, U$4.-VE_1 (-VE), U$4.V37 (-VE), U$4.V38 (-VE), U$4.V39 (-VE), U$4.V40 (-VE), U$4.V41 (-VE), U$4.V42 (-VE), U$4.V43 (-VE), U$4.V44 (-VE), U$4.V45 (-VE), U$4.V46 (-VE), U$4.V47 (-VE), U$4.V48 (-VE), U$4.V49 (-VE), U$4.V50 (-VE), U$4.V51 (-VE), U$4.V52 (-VE), U$4.V53 (-VE), U$4.V54 (-VE), U$4.V55 (-VE), U$4.V56 (-VE), X2.3, X2.4, X3.3, X3.4, X4.3, X4.4, X5.4, X6.4
unnamed: R17.1, R18.1, R19.1, U$2.2 (IN1-)
unnamed: R20.1, R21.2, U$2.6 (IN2-)
unnamed: R17.2, R21.1, U$2.1 (OUT1)
unnamed: C36.1, U4.7 (BOOT)
unnamed: C36.2, I4.P$1 (1), U4.8 (SW)
unnamed: C35.1, R13.2, R15.1, U4.5 (FB)
unnamed: C28.2, R16.2, U4.6 (VCC)
unnamed: R16.1, U4.4 (PG)
unnamed: LED4.A, R14.1
unnamed: C18.1, U2.7 (BOOT)
unnamed: C18.2, I2.P$1 (1), U2.8 (SW)
unnamed: C17.1, R5.2, R7.1, U2.5 (FB)
unnamed: C10.2, R8.2, U2.6 (VCC)
unnamed: R8.1, U2.4 (PG)
unnamed: LED2.A, R6.1
unnamed: C27.1, U3.7 (BOOT)
unnamed: C27.2, I3.P$1 (1), U3.8 (SW)
unnamed: C26.1, R9.2, R11.1, U3.5 (FB)
unnamed: C19.2, R12.2, U3.6 (VCC)
unnamed: R12.1, U3.4 (PG)
unnamed: LED3.A, R10.1
unnamed: C9.1, U1.7 (BOOT)
unnamed: C9.2, I1.P$1 (1), U1.8 (SW)
unnamed: C8.1, R1.2, R3.1, U1.5 (FB)
unnamed: C1.2, R4.2, U1.6 (VCC)
unnamed: R4.1, U1.4 (PG)
unnamed: LED1.A, R2.1
S1: R18.2, R22.1, X5.2
S2: R19.2, X6.2
SO: R20.2, R22.2, U$2.7 (OUT2), U$3.P$3 (3)
VIN: C2.2, C4.1, C5.1, C11.2, C13.1, C14.1, C20.2, C22.1, C23.1, C29.2, C31.1, C32.1, U1.2 (VIN), U1.3 (EN), U2.2 (VIN), U2.3 (EN), U3.2 (VIN), U3.3 (EN), U4.2 (VIN), U4.3 (EN), U$1.P$1 (K)
VO: U$3.P$4 (4), X1.1, X1.2, X5.3
V_PWR: U$1.P$2 (A1), U$1.P$3 (A2), U$4.+VE, U$4.+VE_1 (+VE), U$4.V7 (+VE), U$4.V8 (+VE), U$4.V9 (+VE), U$4.V10 (+VE), U$4.V11 (+VE), U$4.V12 (+VE), U$4.V13 (+VE), U$4.V14 (+VE), U$4.V15 (+VE), U$4.V16 (+VE), U$4.V17 (+VE), U$4.V18 (+VE), U$4.V19 (+VE), U$4.V20 (+VE), U$4.V21 (+VE), U$4.V22 (+VE), U$4.V23 (+VE), U$4.V24 (+VE), U$4.V25 (+VE), U$4.V26 (+VE)

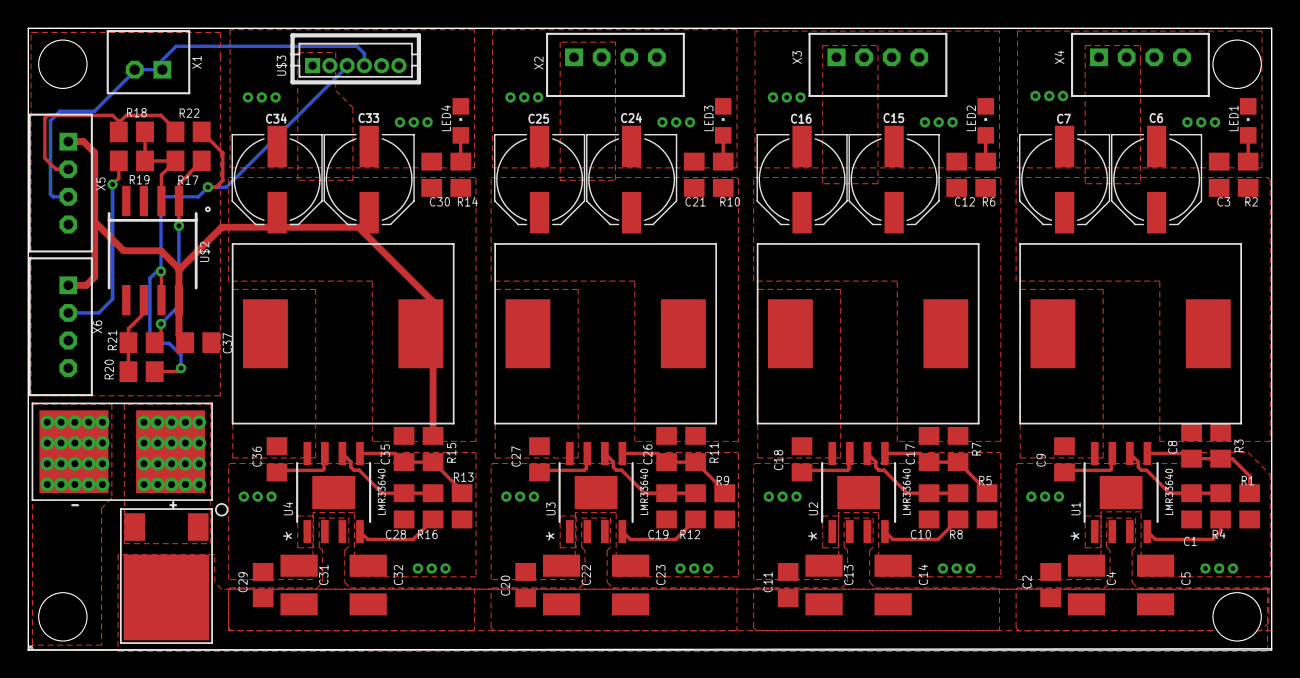
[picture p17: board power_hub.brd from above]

Board: 2 copper layers, 90.0 x 45.0 mm, 81 parts (0 on the bottom side), 38 nets.

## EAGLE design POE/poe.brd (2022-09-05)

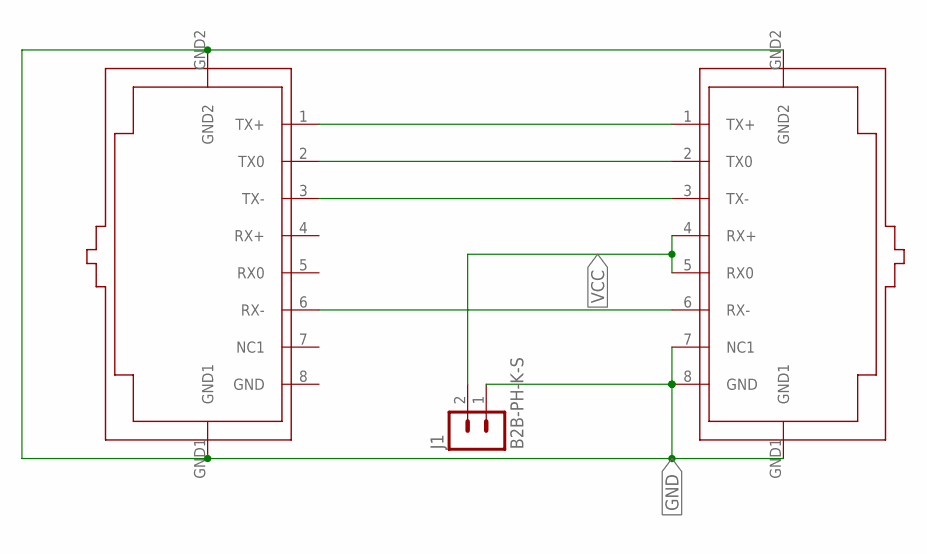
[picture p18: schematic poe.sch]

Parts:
J1: B2B-PH-K-S
U$1, U$2: RJ45-TRAFO

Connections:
GND: J1.1, U$1.GND1, U$1.GND2, U$2.7 (NC1), U$2.8 (GND), U$2.GND1, U$2.GND2
unnamed: U$1.1 (TX+), U$2.1 (TX+)
unnamed: U$1.2 (TX0), U$2.2 (TX0)
unnamed: U$1.3 (TX-), U$2.3 (TX-)
unnamed: U$1.6 (RX-), U$2.6 (RX-)
VCC: J1.2, U$2.4 (RX+), U$2.5 (RX0)

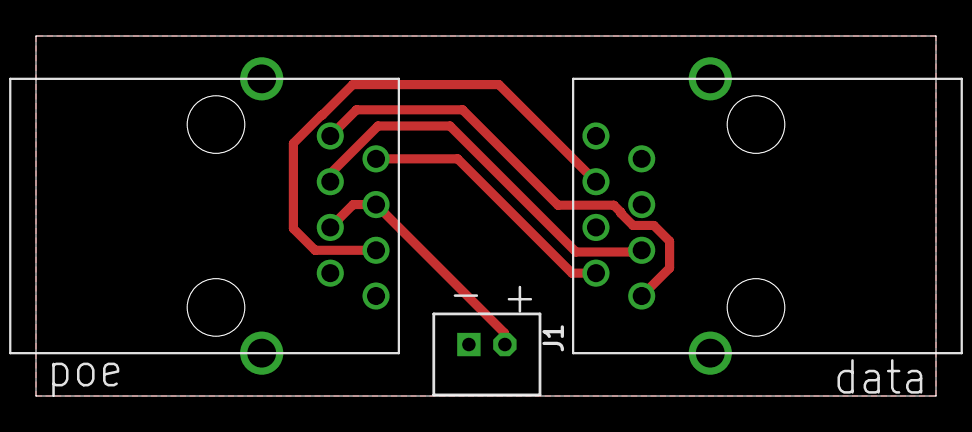
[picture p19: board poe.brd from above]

Board: 2 copper layers, 50.0 x 20.0 mm, 3 parts (0 on the bottom side), 6 nets.

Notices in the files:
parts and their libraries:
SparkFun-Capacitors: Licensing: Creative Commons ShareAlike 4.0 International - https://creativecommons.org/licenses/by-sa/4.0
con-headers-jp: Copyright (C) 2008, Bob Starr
